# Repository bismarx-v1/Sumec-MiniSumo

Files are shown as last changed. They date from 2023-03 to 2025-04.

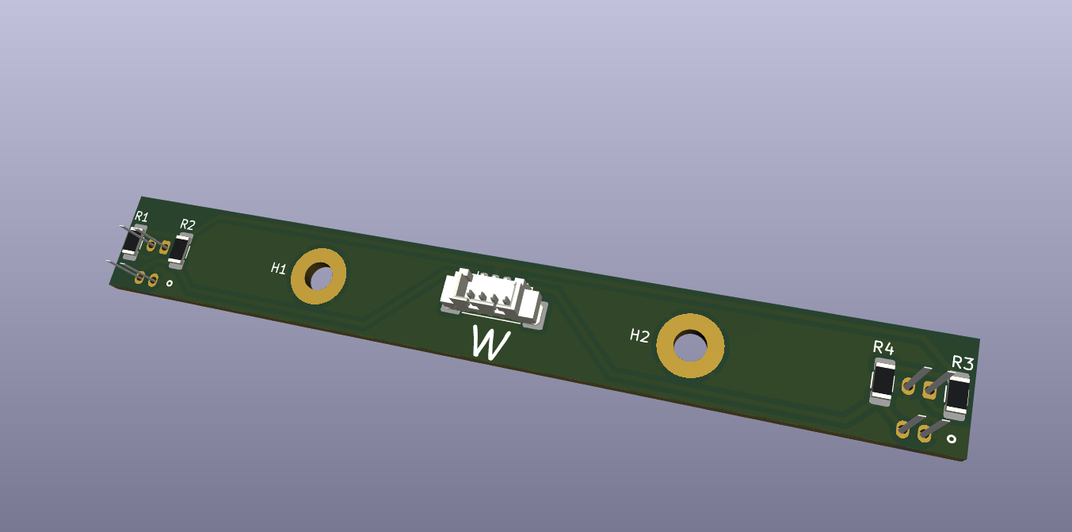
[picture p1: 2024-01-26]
-3D-/el._parts/PCBs/QRE MiniBoards/3D MiniBoards.png

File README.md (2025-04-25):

# THIS IS REPO IS OLD, FOR NEWEST RELAESES VISIT: [Updated repo](https://github.com/bismarx-v1/Sumec-Minisumo-main)

# MiniSumo "SUMEC" Robot Project

## Description
This GitHub repository contains the code and documentation about student-built MiniSumo robot "SUMEC". MiniSumo robots are small autonomous robots designed to compete in MiniSumo competitions, where they attempt to push their opponents out of a ring. Our other repository "Sumec-Remote" is a forked repo from p1rse, created for our own MiniSumo start remote, PCB is ours, schematic was copied from "p1rse/robot-sumo-start-module".
## Contents
- **-3D-** Provides CAD files for the mechanical components of the robot, such as the chassis and sensor mounts.
  
- **-CODE-** Contains the source code for the MiniSumo robot, including firmware for microcontrollers, sensor libraries and control diagrams.
  
- **-DOCS-** Includes robot documentation, rules for specific tournaments, and extras.

- **-PCB-** Includes PCB files, we are using KiCAD for PCB designing.

## Our suppliers
We buy our components from: 

- [Mouser Electronics](https://cz.mouser.com/?utm_id=93841169&gad_source=1)
- [GM Electronics](https://www.gme.cz)
- [TME](https://www.tme.eu/cz/en/)
- [BotLand](https://botland.cz/?gad_source=1)

## Contributing
Contributions to this project are welcome! If you have improvements, bug fixes, or new features to contribute, feel free to contact us!

## Acknowledgements
We would like to thank our school SPŠ na Proseku, our teachers, our principle, for providing resources, knowledge and top-notch equipment.

## Contact
If you have any questions, suggestions, or issues regarding this project, please feel free to contact us: 

Email - savvapopov1804@gmail.com
LinkedIn - www.linkedin.com/in/savva-popov

And follow us on the social media! 
Instagram - @sumec_minisumo_bot

**Sending love, from Czech Republic!**

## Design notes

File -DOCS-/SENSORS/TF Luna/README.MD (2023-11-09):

Configuration input:

GND: I2C
NC/3V3: UART

I2C default address: 0x10 (can be changed)

https://github.com/budryerson/TFLuna-I2C

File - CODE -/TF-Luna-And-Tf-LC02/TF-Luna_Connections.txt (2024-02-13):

=============================================================================
┌──────┐	PCBConnector:	Back = J6
│''''''│	Sensor:		Left
└123456┘
-----------------------------------------------------------------------------
1 - SesorSupply	| 5V
2 - SDA		| ProcessorPin_18
3 - SCL		| ProcessorPin_17
4 - GND		| GND
5 - XShut1	| XS1->0R->GND; (XS2->0R->ProcessorPin_40)
6 - [empty]	| [empty]

=============================================================================
┌──────┐	PCBConnector:	Mid = J7
│''''''│	Sensor:		Mid
└123456┘
-----------------------------------------------------------------------------
1 - SesorSupply	| 5V
2 - SDA		| ProcessorPin_18
3 - SCL		| ProcessorPin_17
4 - GND		| GND
5 - XShut2	| XS2->0R->GND; (XS2->0R->ProcessorPin_41)
6 - [empty]	| [empty]

=============================================================================
┌──────┐	PCBConnector:	Front = J9
│''''''│	Sensor:		Right
└123456┘
-----------------------------------------------------------------------------
1 - SesorSupply	| 5V
2 - SDA		| ProcessorPin_18
3 - SCL		| ProcessorPin_17
4 - GND		| GND
5 - XShut3	| XS3->0R->GND; (XS3->ProcessorPin_42)
6 - [empty]	| [empty]

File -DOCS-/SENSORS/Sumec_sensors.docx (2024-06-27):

# SUMEC Optics

1. Distance measurement

2. Presence of objects

# TF-LUNA 1.

LiDAR Range Sensor / ToF

Distance measured: 8m

Communication protocol: UART/I2C

Output: Digital

Technology: Infrared

Input voltage: Vin = 5V

Connector: Molex PicoBlade

TF-LUNA Manual (https://www.waveshare.com/wiki/TF-Luna_LiDAR_Range_Sensor)

PROS:

- We have 3 of them
- Low FoV: 2°
- Accurate
- We know they work

CONS:

- Cost (500/600Kč)
- Dimensions: 35mm*21.25mm*13.5mm
- Blind zone: 20cm – unreliable measurement
- Harder measurement for objects with high reflectivity

# Pololu Distance Sensor 1.

LiDAR-based Distance Sensor / ToF

Distance measured: 50, 130cm

Communication: Digital Pulse Width

Output: Digital

Technology: Infrared laser

Input voltage: Vin = 3-5V

Connector: 2,54 - 3Pad holes

Polulu Pulse Width manual (https://www.pololu.com/product/4071)

PROS:

- Dimensions: (21.6 × 8.9 × 3.5 mm)
- Accurate

CONS:

- Cost: (400Kč)
- Minimum range: 4 cm (for accurate measurement); < 1 mm (for detection)
- High FoV: 15°
- We don’t know if they work

# VL53L1X 1.

Laser distance measurement sensor / ToF

Distance measured: 400cm max

Communication: I2C

Output: Digital

Technology: Infrared laser

Input voltage: Vin = 3-5V

Connector: 2,54 - Pad holes

VL53L1X Datasheet (https://www.laskakit.cz/user/related_files/vl53l1x.pdf)

PROS:

- Cost: (200Kč)
- Dimensions: 29.5x22mm
- Accuracy 1mm

CONS:

- Programmable FoV from 15 to 27 degrees (?)
- We don’t know if they work

# VL53L3CX 1.

Laser distance measurement sensor / ToF

Distance measured: 300cm max

Communication: I2C

Output: Digital

Technology: Infrared laser

Input voltage: Vin = 2.8-5V

Connector: 2,54 - Pad holes

VL53L3CX (https://cz.mouser.com/datasheet/2/389/vl53l3cx-satel-1858618.pdf)

PROS:

- Dimensions:
- True distance measurement independent of target size and reflectance

CONS:

- Cost: (400Kč)
- We don’t know if they work

# TF-LC02 1.

LiDAR laser distance Sensor / ToF

Distance measured: 200cm

Communication: UART

Output: Digital

Technology: Infrared laser

Input voltage: Vin = 3-3.7V

Connector: JST SH

Polulu Pulse Width manual (https://www.pololu.com/product/4071)

PROS:

- We have 1 of them
- Cost: (250Kč)
- Very small size 20 x 11.5 x 7.6 mm
- Accurate

CONS:

- Minimum range: 3 cm (for accurate measurement)
- High FoV: 18°
- We don’t know if they work
- Almost no documentation

# Pololu Digital Distance Sensor 2.

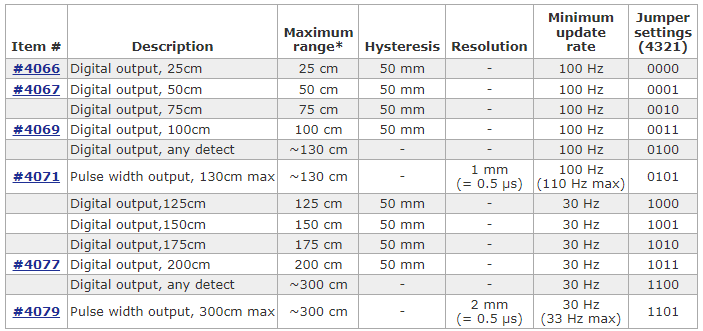
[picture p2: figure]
Obsah obrázku text, snímek obrazovky, číslo, Písmo Popis byl vytvořen automaticky

LiDAR based distance sensor / I/O

Distance measured: 50/100cm

Communication: HIGH/LOW

Output: Digital

Technology: Infrared laser

Input voltage: Vin = 3-5.5V Distance seen is based on the jumper config.

Connector: 2.54, 3 Pad Holes

Polulu digital detection manual (https://www.pololu.com/product/4067)

PROS:

- Size 21.6 × 8.9 × 3.5 mm
- Accurate – 1mm
- Adjustable distance
- Adjustable type of measurement

CONS:

- Cost: (500Kč)
- FoV: 15°
- We don’t know if they work

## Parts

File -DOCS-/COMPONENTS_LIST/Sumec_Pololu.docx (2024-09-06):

# SUMEC Pololu BOM

# Pololu Distance Sensor 1.

LiDAR-based Distance Sensor / ToF

Distance measured: 50, 130cm

Communication: Digital Pulse Width

Output: Digital

Technology: Infrared laser

Input voltage: Vin = 3-5V

Connector: 2,54 - 3Pad holes

Polulu Pulse Width manual (https://www.pololu.com/product/4071)

https://www.pololu.com/product/4064

# 12V 1100RPM HPCB

High power, carbon brushes DC motor

Voltage: 12V

Encoder: Yes (Side)

RPM: 1100

Length: 41mm

Connector: JST SH Female

2X https://www.pololu.com/product/5211

# 12V 650RPM HPCB

High power, carbon brushes DC motor

Voltage: 12V

Encoder: Yes (Side)

RPM: 650

Length: 41mm

Connector: JST SH Female

2x https://www.pololu.com/product/5213

# Pololu Digital Distance Sensor 2.

Obsah obrázku text, snímek obrazovky, číslo, Písmo Popis byl vytvořen automaticky

LiDAR based distance sensor / I/O

Distance measured: 50/100cm

Communication: HIGH/LOW

Output: Digital

Technology: Infrared laser

Input voltage: Vin = 3-5.5V Distance seen is based on the jumper config.

Connector: 2.54, 3 Pad Holes

Polulu digital detection manual (https://www.pololu.com/product/4067)

PROS:

- Size 21.6 × 8.9 × 3.5 mm
- Accurate – 1mm
- Adjustable distance
- Adjustable type of measurement

CONS:

- Cost: (500Kč)
- FoV: 15°
- We don’t know if they work

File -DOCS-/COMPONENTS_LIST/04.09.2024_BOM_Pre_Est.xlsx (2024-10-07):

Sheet: SMD 1206
Footprint | Value | Link | Reserve
1206 | S-DIODE | S-Diode, 2A, 1206, mouser (https://cz.mouser.com/ProductDetail/KYOCERA-AVX/SD1206S040S2R0?qs=jCA%252BPfw4LHbfEJl0sZ31oA%3D%3D) | 1
1206 | 10k |  | 2
1206 | 100R |  | 3
1206 | 15R |  | 5
1206 | 0R |  | 4
1206 | 22uF, Polymer-Tantal | 22uF, 16V, Tantal-Polymer (https://cz.mouser.com/ProductDetail/KYOCERA-AVX/TCJA226M016R0300E?qs=%252B6g0mu59x7JjwGwmiCcXvg%3D%3D) | 6
1206 | 10uF, Polymer-Tantal | 10uF, 25V, Tantal-Polymer (https://cz.mouser.com/ProductDetail/KYOCERA-AVX/TCJA106M025R0150E?qs=hWgE7mdIu5SUx0aLKy2TqQ%3D%3D) | 10
1206 | 10uF, 16V, Tantal | 10uF, 16V, 1206, tantal, mouser (https://cz.mouser.com/ProductDetail/KEMET/T491A106K016AT) | 28 | 6
1206 | 1uF Tantal |  | 8
1206 | 100nF, Ceramic |  | 8

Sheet: SMD 0805
Footprint | Value | Link | Reserve
0805 | RED | Red LED, 20mA 1.9V, 0805, mouser (https://cz.mouser.com/ProductDetail/Stanley-Electric/VFHV1112H-3BZ2B-TR?qs=byeeYqUIh0PKiA%252BYRcKo5Q%3D%3D) | 15
0805 | YELLOW | Yellow LED, 20mA, 1.9V, 0805, mouser (https://cz.mouser.com/ProductDetail/Stanley-Electric/FY1112H-TR?qs=byeeYqUIh0M%2F1I90%252BhjkXg%3D%3D) | 6
0805 | GREEN | Green-Yellow LED, 20mA, 1.9V, mouser (https://cz.mouser.com/ProductDetail/Stanley-Electric/VFHD1112H-3B72B-TR?qs=byeeYqUIh0N1xLw8fV03PA%3D%3D) | 4
0805 | 10k | 10k, 250mW, 0805, mouser (https://cz.mouser.com/ProductDetail/Vishay-Dale/RCC080510K0FKEA?qs=GedFDFLaBXGY93oge9hajw%3D%3D) | <60
0805 | 1k | 1k. 500mW, 0805, mouser (https://cz.mouser.com/ProductDetail/Vishay-Dale/CRCW08051K00FKEAHP?qs=FlFvgi4rxBy%252Bn2DMV%2FkIbA%3D%3D) | 2
0805 | 560R | 560R, 500mW, 0805, mouser (https://cz.mouser.com/ProductDetail/Bourns/CHP0805AFX-5600ELF?qs=GedFDFLaBXHiLkJv9wkGiw%3D%3D) | 18
0805 | 100R | 100R, 0.5W, 0805, mouser (https://cz.mouser.com/ProductDetail/Vishay-Dale/CRCW0805100RFKEAHP?qs=k2%2FDWSARqgHN0DmoUSjg4g%3D%3D) | 10
0805 | 200R | 200R, 500mW, 0805, mouser (https://cz.mouser.com/ProductDetail/Vishay-Dale/CRCW0805200RFKEAHP?qs=2Xec%252BEQj5n%252BcRsKDNXpbZw%3D%3D) | 4
0805 | 15R | 15R, 100mW, 0805,mouser (https://cz.mouser.com/ProductDetail/Panasonic/ERJ-6RED15R0V?qs=KTDjhDDUMAl6Ra4%2FZLG24g%3D%3D) | 16
0805 | 2.2R | 2.2R, 500mW, 0805, mouser (https://cz.mouser.com/ProductDetail/Vishay-Dale/CRCW08052R20FKEAHP?qs=40TFAHZMFvc8altFjF5kRw%3D%3D) | 4
0805 | 100nF | 100nF, 16V, 0805, ceramic, mouser X7R (https://cz.mouser.com/ProductDetail/YAGEO/AC0805KRX7R7BB104) | >60
0805 | 22nF | 22nF, 50V, 0805, ceramic, mouser, X7R (https://cz.mouser.com/ProductDetail/KYOCERA-AVX/08055C223KAT4A)
0805 | 18pF | 18pF, 16V, 0805, ceramic, mouser (https://cz.mouser.com/ProductDetail/KYOCERA-AVX/0805YA180JAT2A?qs=nl0EtZFOfLiGc7H%252BYUnNHw%3D%3D) | 5

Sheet: SMD OTHER
Value | Footprint | Link | Reserve
Conn_01x04_Pin | Molex_PicoBlade_1x04-1MP_P1.25mm_Vertical | Molex PicoBlade, 4 Pin, vertical, mouser | 2
Conn_01x03_Pin | Molex_PicoBlade_1x03-1MP_P1.25mm_Vertical | Molex PicoBlade, 3 Pin, vertical, mouser | 4
Conn_01x06_Pin | Molex_PicoBlade_1x06-1MP_P1.25mm_Vertical | Molex PicoBlade, 6 Pin, vertical, mouser | 1
Conn_01x04_Pin | Molex_PicoBlade_1x04-1MP_P1.25mm_Horizontal | Molex PicoBlade, 4 Pin, horizontal, mouser | 2
TYPE-C-31-M-12 | USB_Type_C | USB C mouser (https://eu.mouser.com/ProductDetail/GCT/USB4105-GF-A-060?qs=QNEnbhJQKvY2mocwNJzgfA%3D%3D) | 4
5V, 5A | TO-252, AZ1084 |  | 2
3V3, 3A | LD1085 |  | 2
LM1084-3.3 | TO-263-3_TabPin2 | LM1084IS-3.3-NOPB, mouser
LM1084-5.0 | TO-263-3_TabPin2 | LM1084IS-5.0-NOPB, mouser
USBLC6-2SC6 | TSOT-23-6_HandSoldering | ESD protekce mouser | 6
SW_Push | SW_SPST_B3U-1000P | B3U-1000P mouser (https://cz.mouser.com/ProductDetail/Omron-Electronics/B3U-1000P?qs=AO7BQMcsEu4ip80xyf2FwA%3D%3D) | 6
QRE1113 | OnSemi_CASE100AQ - QRE1113 | QRE1113 THT mouser (https://cz.mouser.com/ProductDetail/onsemi-Fairchild/QRE1113?qs=ne66E0WZ%2FFkJiYCW1J5zEw%3D%3D) | 10
QRE1113_SMD | QRE1113_SMD |  | 10
MCU | ESP32-S3-WROOM-1 | ESP32 S3 WROOM1 mouser (https://cz.mouser.com/ProductDetail/Espressif-Systems/ESP32-S3-WROOM-1-N4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) | 1
MCU | ESP32-S3-WROOM-2 |  | 3
TB6612FNG | TB6612FNG |  | 8
DRV8874 | DRV8874PWPR | DRV8874. mouser (https://cz.mouser.com/ProductDetail/Texas-Instruments/DRV8874PWPR?qs=mAH9sUMRCtvh%2FSU15ywmDA%3D%3D) | 0
DMG6968U-7 | TSOT-23-3_HandSoldering | NMOS, SOT23-3, mouser (https://eu.mouser.com/ProductDetail/Diodes-Incorporated/DMG6968U-7?qs=oUsD4qhOtFxfxyoeWY4RMA%3D%3D) | 6
DS04-254-1-05BK-SMT | DIP_SWITCH | 5P, 2.54mm, DIP, mouser (https://cz.mouser.com/ProductDetail/CUI-Devices/DS04-254-1-05BK-SMT?qs=wnTfsH77Xs5Ndj%252Bt08dChA%3D%3D) | 1
Crystal - ABM8G | CRYSTAL_SMD | 16 MHz, 18 pF, mouser (https://www.mouser.co.uk/ProductDetail/ABRACON/ABM8G-16.000MHZ-18-D2Y-T?qs=3LVMET7lfiPkoUdIbdKAPg%3D%3D) | 4
YC248-JR-0710KL | RESISTOR_ARRAY | 10k, 8x0402, mouser (https://cz.mouser.com/ProductDetail/YAGEO/YC248-JR-0710KL?qs=8cPjvKtxWv7XgZyJevtvWg%3D%3D) | 8

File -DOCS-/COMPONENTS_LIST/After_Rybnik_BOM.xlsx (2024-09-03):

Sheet: SMD 1206
Footprint | Value | Link | Reserve
1206 | 10k |  | 2
1206 | 100R |  | 3
1206 | 15R |  | 6
1206 | 0R |  | 7
1206 | 10uF? Tantal |  | 10
1206 | 10uF, Ceramic |  | 6
1206 | 10uF, 16V, Tantal | 10uF, 16V, 1206, tantal, mouser (https://cz.mouser.com/ProductDetail/KEMET/T491A106K016AT) | <30
1206 | 1uF Tantal |  | 7
1206 | 100nF |  | 9
1206 | s-diode | S-Diode, 2A, 1206, mouser (https://cz.mouser.com/ProductDetail/KYOCERA-AVX/SD1206S040S2R0?qs=jCA%252BPfw4LHbfEJl0sZ31oA%3D%3D) | 4

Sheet: SMD 0805
Footprint | Value | Link | Reserve
805 | 10k | 10k, 250mW, 0805, mouser (https://cz.mouser.com/ProductDetail/Vishay-Dale/RCC080510K0FKEA?qs=GedFDFLaBXGY93oge9hajw%3D%3D) | 12
805 | 560R | 560R, 500mW, 0805, mouser (https://cz.mouser.com/ProductDetail/Bourns/CHP0805AFX-5600ELF?qs=GedFDFLaBXHiLkJv9wkGiw%3D%3D) | 18
805 | 100R | 100R, 0.5W, 0805, mouser (https://cz.mouser.com/ProductDetail/Vishay-Dale/CRCW0805100RFKEAHP?qs=k2%2FDWSARqgHN0DmoUSjg4g%3D%3D) | 10
805 | 15R | 15R, 100mW, 0805,mouser (https://cz.mouser.com/ProductDetail/Panasonic/ERJ-6RED15R0V?qs=KTDjhDDUMAl6Ra4%2FZLG24g%3D%3D) | 16
805 | 22nF, 50V Ceramic | 22nF, 50V, 0805, ceramic, mouser, X7R (https://cz.mouser.com/ProductDetail/KYOCERA-AVX/08055C223KAT4A) | 15
805 | 100nF, 16V, Ceramic | 100nF, 16V, 0805, ceramic, mouser X7R (https://cz.mouser.com/ProductDetail/YAGEO/AC0805KRX7R7BB104) | <80
805 | RED | Red LED, 20mA 1.9V, 0805, mouser (https://cz.mouser.com/ProductDetail/Stanley-Electric/VFHV1112H-3BZ2B-TR?qs=byeeYqUIh0PKiA%252BYRcKo5Q%3D%3D)
805 | YELLOW | Yellow LED, 20mA, 1.9V, 0805, mouser (https://cz.mouser.com/ProductDetail/Stanley-Electric/FY1112H-TR?qs=byeeYqUIh0M%2F1I90%252BhjkXg%3D%3D) |  | 8,8,18
805 | GREEN-YELLOW | Green-Yellow LED, 20mA, 1.9V, mouser (https://cz.mouser.com/ProductDetail/Stanley-Electric/VFHD1112H-3B72B-TR?qs=byeeYqUIh0N1xLw8fV03PA%3D%3D)

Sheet: SMD OTHER
Footprint | Value | Link | Reserve
Molex_PicoBlade_53398-0471_1x04-1MP_P1.25mm_Vertical | Conn_01x04_Pin | Molex PicoBlade, 4 Pin, vertical, mouser | 2
Molex_PicoBlade_53398-0371_1x03-1MP_P1.25mm_Vertical | Conn_01x03_Pin | Molex PicoBlade, 3 Pin, vertical, mouser | 4
Molex_PicoBlade_53398-0671_1x06-1MP_P1.25mm_Vertical | Conn_01x06_Pin | Molex PicoBlade, 6 Pin, vertical, mouser | 1
Molex_PicoBlade_53261-0471_1x04-1MP_P1.25mm_Horizontal | Conn_01x04_Pin | Molex PicoBlade, 4 Pin, horizontal, mouser | 2
USB_Type_C | TYPE-C-31-M-12 | USB C mouser | 6
TO-252 | 5V, 5A max 12V |  | 2
LD1085 | 3v3, 3A |  | 2
TO-263-3_TabPin2 | LM1084-3.3 | LM1084IS-3.3-NOPB, mouser | 1
TO-263-3_TabPin2 | LM1084-5.0 | LM1084IS-5.0-NOPB, mouser | 1
TSOT-23-6_HandSoldering | USBLC6-2SC6 | ESD protekce mouser
ESP32-S3-WROOM-1 | ESP32-S3-WROOM-1 | ESP32 S3 WROOM1 mouser (https://cz.mouser.com/ProductDetail/Espressif-Systems/ESP32-S3-WROOM-1-N4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) | 1
DRV8874 | DRV8874PWPR | DRV8874. mouser (https://cz.mouser.com/ProductDetail/Texas-Instruments/DRV8874PWPR?qs=mAH9sUMRCtvh%2FSU15ywmDA%3D%3D) | 1
esp32 s3 wroom2 | esp32 s3 wroom2 |  | 3
SW_SPST_B3U-1000P | SW_Push | B3U-1000P mouser (https://cz.mouser.com/ProductDetail/Omron-Electronics/B3U-1000P?qs=AO7BQMcsEu4ip80xyf2FwA%3D%3D) | 6
OnSemi_CASE100AQ - QRE1113 | QRE1113 | QRE1113 THT mouser (https://cz.mouser.com/ProductDetail/onsemi-Fairchild/QRE1113?qs=ne66E0WZ%2FFkJiYCW1J5zEw%3D%3D) | 6
qre smd | qresmd |  | 10
TB6612FNG |  |  | 8

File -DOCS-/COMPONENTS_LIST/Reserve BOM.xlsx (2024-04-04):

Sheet: el. components - THD
EL. COMPONENTS
QTY in use | QTY reserve | lost | NAME | VALUE | CODE | COST (1pc) | SUPPLIER
2 | 1 |  | stabilizer | 3v3 3a | lm1085
0 | 3 |  | stabilizer | 3v3 5a | lm1084 |  |  | 1
 | 2 |  | stabilizer | 3v3 1a | ld1117av33 |  |  | 1
0 | 4 |  | stabilizer | 5v 1a5 | UA7805C
0 | 3 |  | stabilizer | 3v3 0,8a | ld33v |  |  | 1
 | 21 |  | resistor | 10k
 | 16 |  | resistor | 100
 |  |  | resistor | 82
 |  |  | resistor | 68
 | 14 |  | cappacitor | 0,1µF 100V |  |  |  | 1
 | 12 |  | cappacitor | 10µF 16V |  |  |  | 1
 | 11 |  | cappacitor | 22µF 16V |  |  |  | 1
 | 5 |  | schottky diode | 1A |  |  |  | 1
 | 5 |  | schottky diode | 3A |  |  |  | 1
 | 13 |  | LED | multi color
6 | 4 |  | button
1 | 2 |  | ir recever |  | tsop382
6 | 2 |  | laser sensor
8 | 19 |  | qre tht
 | 6 |  | 3pin conector M
 | 6 |  | 3pin conector F
0 | 3 |  | ir recever | 2,5-5,5V 38kH | TSOP31138 |  | mouser | 1
0 | 1 |  | usb-c 4-pin
0 | 2 |  | regulátor nap. | 5V 3A pos. | ld1085V50 |  | mouser
 |  |  | mosfet |  | irf520 |  |  | 1

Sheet: el. components - SMD
EL. COMPONENTS
QTY in use | QTY reserve | lost | NAME | VALUE | CODE | COST (1pc) | SUPPLIER
 | ? | 1 | esp32 s3 vrum1
 | 3 |  | esp32 s3 vrum2 |  |  |  |  | 1
 | 8 | 1 | brush motor driver |  | TB6612FNG |  | mouser | 1
 | 1 |  | h-bridge m |  | drv8874pwpr |  | mouser | 1
 | 6 | 1 | elektrostatická ochrana |  | USBLC6-2SC6 |  | mouser | 1
0 | 10 |  | tantalový kondenzátor | 25V 106 20% | TCJA106M025R0150E |  | mouser | 1
 | 6 |  | tantalový kondenzátor | 16V 226 20% | TCJA226M016R0300E |  | mouser | 1
 | 8 |  | tantalový kondenzátor | 16V 1µF | T491A105K016AT |  | mouser | 1
 | 45 |  | tantalový kondenzátor | 16V 10µF |  |  | mouser | 1
 | 6 |  | keramický kondenzátor | 16v 10µF | KAF31GR71C106KU |  | mouser | 1
 | ? |  | keramický kondenzátor | 25V 100nF | 12063C104JAT2A |  | mouser
 |  |  | keramický kondenzátor | 50v 22nf | 08055c223kat4a |  | mouser | 1
 | cca 98 |  | keramický kondenzátor | 16v 0,1µF | ac0805krx7r7bb104 |  | mouser | 1
0 | 1 |  | laserowy czujnik |  | TF-LC02 |  |  | 1
 | 6 |  | čudlíci NO |  | b3u-1000p |  | mouser | 1
 | 4 |  | JST SH 1mm 6-pin konektor 90°
 | 10 |  | JST SH 1mm 6-pin konektor rovný
 | 4 |  | shotkyho dioda |  | CD1206-B260 |  | mouser | 1
 | 7 |  | rezistor | 0Ω | CRCW12060000ZSTC |  | mouser | 1
 | ? |  | rezistor | 100Ω 0,25W .1% | RT1206BRD07100RL |  | mouser
 | 2 |  | tenkovrství rezistor | 10kΩ | ERA-8BRB1002V |  | mouser | 1
 | 3 |  | tenkovrství rezistor | 100kΩ | tr1206brd07100rt |  | mouser | 1
 | 16 |  | tlustovrství rezistor | 15r | erj-6red15r0v |  | mouser | 1
 | 18 |  | tlustovrství rezistor | 650r | chpp0805afx-5600elf |  | mouser | 1
 | 10 |  | tlustovrství rezistor | 100Ω 0,5W 1% | crcw0805100rfkeahp |  | mouser | 1
 | 6 |  | tlustovrství rezistor | 150Ω 0,25W 5% | AC1206JR-0715RL |  | mouser | 1
 | 12 |  | tlustovrství rezistor | 10k .25w 1% | rcc080510k0fkea |  | mouser | 1
a | 10 |  | qre |  | qre1113 |  |  | 1
 | 5 | 1 | USB-C - F |  |  |  |  | 1
2 | 2 |  | tranzistor | 20v | TSM2302CX RF |  |  | 1
 | 1 |  | stabilizer | 5v 5a | lm1084 |  |  | 1
 | 1 |  | stabilizer | 3v3 5a | lm1084-3v3 |  |  | 1
0 | 2 |  | regulátor nap. | 3.3V 3A pos. | LD1085D2M33R |  | mouser | 1
 | 2 | 1 | regulátor nap. |  | AZ1084CD-5.0TRG1 |  | mouser | 1
 | 10 |  | LED | red | vfhd1112h-3b72b-tr |  | mouser | 1
 | 18 |  | LED |  | vfhv1112h-3bz2b-tr |  | mouser | 1
 | 8 |  | LED | yellow | fy1112hh-tr |  | mouser | 1
 | 1 |  | PicoBlade | 6p. 1.25 F | 53368-4006 |  | mouser | 1
 | 4 |  | PicoBlade | 3p. 1.25 F | 53398-4003 |  | mouser | 1
 | 2 |  | PicoBlade - flat | 4p. 1.25 F | 53261- |  | mouser | 1

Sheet: el. components - other
EL. COMPONENTS
QTY in use | QTY reserve | lost | NAME | VALUE | CODE | COST (1pc) | SUPPLIER
0 | 1 |  | esp32-s3-devkitC-1
0 | 4 |  | H bridge
1 | 1 |  | esp32-vrum32-devkit-1
0 | 1 |  | arduino UNO
0 | 1 |  | arduino NANO
1 | 2 | 2 | circuit board mk2
3 | 2 |  | XT-30 M
4 | 6 |  | XT-30 F
0 | 1 |  | jet switch
0 | 2 |  | lever switch
2 | 1 |  | switch screwable | 2A
3 | 2 |  | switch
 | 4 |  | DC motor | 12V 150rpm
 | 4 |  | DC motor | 12V 300rpm
 | 0 |  | battery | 8,4v 450mAh
 | 1 |  | battery | 12,6V 450mAh
 | 1 |  | terrorist battery 2s | ???
 | 3 |  | TF-Luna | 5V
 |  |  | 0

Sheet: mechanics
MECHANICS
QTY in use | QTY reserve | lost | NAME | VALUE | CODE | COST (1pc) | SUPPLIER
2 |  |  | jsumo wheel - core
2 |  |  | jsumo wheel - tire
2 |  |  | custom wheels - core
 | 30 |  | heta isert | M3
 | 2 |  | všesměrová koule

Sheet: tools + other
TOOLS
QTY in use | QTY reserve | lost | NAME | VALUE | CODE | COST (1pc) | SUPPLIER
1 |  |  | battery tester
1 |  |  | IR controller
 | 1 |  | USB-A na USB-B kabel
 | 1 |  | posuvné měřítko
 |  |  | li-pol guard
 |  |  | thermal compound
 | 1 |  | t10 klíč
 | 3 |  | cr2025 batt

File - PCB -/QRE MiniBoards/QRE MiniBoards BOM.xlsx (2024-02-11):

Item | Reference(s) | Footprint | Qty | Value | Supplier and ref
1 | H1,H2 | MountingHole_3.2mm_M3_Pad | 2 | M3
2 | R3,R1 | R_0805_2012Metric_Pad1.20x1.40mm_HandSolder | 2 | 100
3 | R4,R2 | R_0805_2012Metric_Pad1.20x1.40mm_HandSolder | 2 | 10k
4 | J2 | Molex_PicoBlade_53261-0471_1x04-1MP_P1.25mm_Horizontal | 1 | Conn_01x04_Pin
5 | U2,U1 | OnSemi_CASE100AQ - QRE1113 | 2 | QRE1113
 |  |  | 9

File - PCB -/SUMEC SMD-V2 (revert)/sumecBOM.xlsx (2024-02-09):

Id | Designator | Footprint | Quantity | Designation | Supplier and ref
1 | IC2,IC3 | DRV8874 | 2 | DRV8874PWPR
2 | SW1,SW3,SW2 | SW_SPST_B3U-1000P | 3 | SW_Push
3 | R3 | R2D2 | 1 | R
4 | H1,H3,H2 | MountingHole_3.2mm_M3_Pad | 3 | MountingHole_Pad
5 | J2 | SolderWire-0.1sqmm_1x01_D0.4mm_OD1mm | 1 | Conn_01x01_Pin
6 | U4 | TO-263-3_TabPin2 | 1 | LM1084-5.0
7 | C18,C1 | C_0805_2012Metric_Pad1.18x1.45mm_HandSolder | 2 | 22nF.hb
8 | C17,C6 | C_0805_2012Metric_Pad1.18x1.45mm_HandSolder | 2 | 100nF.hb
9 | C13,C11,C12,C10 | CP_EIA-2012-12_Kemet-R_Pad1.30x1.05mm_HandSolder | 4 | 10uF.stabl
10 | R2,R1 | R_0805_2012Metric_Pad1.20x1.40mm_HandSolder | 2 | 220
11 | J5 | USB_Type_C | 1 | TYPE-C-31-M-12
12 | C7 | C_0805_2012Metric_Pad1.18x1.45mm_HandSolder | 1 | 100nF.en
13 | C16,C5 | CP_EIA-2012-12_Kemet-R_Pad1.30x1.05mm_HandSolder | 2 | 10uF.hb
14 | D3 | D_0805_2012Metric_Pad1.15x1.40mm_HandSolder | 1 | D_Schottky
15 | R7 | R_0805_2012Metric_Pad1.20x1.40mm_HandSolder | 1 | 10k.mcu
16 | R6,R5 | R_0805_2012Metric_Pad1.20x1.40mm_HandSolder | 2 | 15R
17 | D2,D1 | LED_0805_2012Metric_Pad1.15x1.40mm_HandSolder | 2 | LED
18 | U1 | TO-263-3_TabPin2 | 1 | LM1084-3.3
19 | C9 | C_0805_2012Metric_Pad1.18x1.45mm_HandSolder | 1 | 100nF
20 | J7,J6,J8 | Molex_PicoBlade_53398-0671_1x06-1MP_P1.25mm_Vertical | 3 | Conn_01x06_Pin
21 | IC1 | XT30U-M_1x02_P5.0mm_Vertical | 1 | XT30U-F
22 | U3 | TSOT-23-6_HandSoldering | 1 | USBLC6-2SC6
23 | U2 | ESP32-S3-WROOM-1 | 1 | ESP32-S3-WROOM-1
24 | U5 | TSOP | 1 | TSOP382xx
25 | R8 | Logo | 1 | R
26 | C8 | C_0805_2012Metric_Pad1.18x1.45mm_HandSolder | 1 | 100nF.boot
27 | SW4 | Custom_SPDT_4.8mm_Switch | 1 | SW_DPDT_x2
28 | C3 | CP_EIA-2012-12_Kemet-R_Pad1.30x1.05mm_HandSolder | 1 | 10uF.mcu
29 | J4,J10,J9 | Molex_PicoBlade_53398-0371_1x03-1MP_P1.25mm_Vertical | 3 | Conn_01x03_Pin
30 | C4 | C_0805_2012Metric_Pad1.18x1.45mm_HandSolder | 1 | 100nF.mcu
31 | R4 | R_0805_2012Metric_Pad1.20x1.40mm_HandSolder | 1 | 0R
32 | C19,C2 | C_0805_2012Metric_Pad1.18x1.45mm_HandSolder | 2 | 220nF.hb
33 | J1 | JST_XH_B4B-XH-A_1x04_P2.50mm_Vertical | 1 | Conn_01x04_Pin
34 | C15,C14 | CP_EIA-2012-12_Kemet-R_Pad1.30x1.05mm_HandSolder | 2 | 10uF.shrp
35 | R9 | R_0805_2012Metric_Pad1.20x1.40mm_HandSolder | 1 | 10k
36 | J3 | Molex_PicoBlade_53398-0471_1x04-1MP_P1.25mm_Vertical | 1 | Conn_01x04_Pin
37 | R10 | R_0805_2012Metric_Pad1.20x1.40mm_HandSolder | 1 | 100

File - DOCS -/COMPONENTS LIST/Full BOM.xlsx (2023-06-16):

QTY | VALUE | COMPONENT | COST | DO WE HAVE IT?
2 | 10uF | Cappacitor |  | 9
1 | RED | LED | 0 | YES
1 | D_Schottky | Diode |  | 2
3 | M3 | Mounting Hole |  | 30
1 | XT30U-F | Battery conneector |  | 2F and 2M
1 | 75 | Resistor
4 | 100 | Resistor |  | 6
4 | 10k | Resistor |  | 10
1 | SW_SPDT | Switch (3 pin header) |  | 2 types 8 in total
1 | SW_Push | Button | 0 | YES
1 | ESP32-DEVKIT-V1 | MCU |  | 3
3 | VL53L0X | Laser Sensor |  | 4
1 | TSOP382xx | IR Sensor |  | 1 module,
4 | QRE1113 | Line Rensor |  | 10 smd 11 thd
1 | LD1117AV33 | Stabiliastor |  | 2
1 | ROB-14450 | Motor Driver |  | 4+1
15x2 | 2,54mm | Pin Header
8x2 | 2,54mm | Pin Header
3 | CUSTOM MADE | Laser sensor connector
2 | 12V 150/300/500 RPM | DC Motors |  | 8
1 | 450mAh, 12,6V full charge | Battery/Terrorist battery |  | 1+1
2 | JSUMO | Silicon wheels |  | 3
2 | JSUMO/Custom made | Aluminuim wheels |  | 2+2
1 | Tester | Battery Tester |  | 1

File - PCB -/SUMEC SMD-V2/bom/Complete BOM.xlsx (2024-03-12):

Id | Designator | Quantity | Footprint | Value | Link | Reserve | Quantity
1 | R3 | 1 | R_0805_2012Metric_Pad1.20x1.40mm_HandSolder | 560R | 560R, 500mW, 0805, mouser (https://cz.mouser.com/ProductDetail/Bourns/CHP0805AFX-5600ELF?qs=GedFDFLaBXHiLkJv9wkGiw%3D%3D) | 20 | 1
2 | R5 | 1 | R_1206_3216Metric_Pad1.30x1.75mm_HandSolder | 0R | 0R, 250mW, 1206, mouser (https://cz.mouser.com/ProductDetail/Vishay-Dale/CRCW12060000ZSTC?qs=y5m63dMNjqu0KlgPSWR0ZQ%3D%3D) | 14 | 1
3 | R7,R6 | 2 | R_0805_2012Metric_Pad1.20x1.40mm_HandSolder | 15R | 15R, 100mW, 0805,mouser (https://cz.mouser.com/ProductDetail/Panasonic/ERJ-6RED15R0V?qs=KTDjhDDUMAl6Ra4%2FZLG24g%3D%3D) | 20 | 2
4 | R9,R8 - R4,R2 | 4 | R_0805_2012Metric_Pad1.20x1.40mm_HandSolder | 10k | 10k, 250mW, 0805, mouser (https://cz.mouser.com/ProductDetail/Vishay-Dale/RCC080510K0FKEA?qs=GedFDFLaBXGY93oge9hajw%3D%3D) | 20 | 4
5 | R1,R2,R10 - R3,R1 | 5 | R_0805_2012Metric_Pad1.20x1.40mm_HandSolder | 100R | 100R, 0.5W, 0805, mouser (https://cz.mouser.com/ProductDetail/Vishay-Dale/CRCW0805100RFKEAHP?qs=k2%2FDWSARqgHN0DmoUSjg4g%3D%3D) | 20 | 5
6 | R20, R21 | 2 | R2D2, Logo | R |  |  | 2
7 | C3,C4 | 2 | C_0805_2012Metric_Pad1.18x1.45mm_HandSolder | 22nF.hb | 22nF, 50V, 0805, ceramic, mouser, X7R (https://cz.mouser.com/ProductDetail/KYOCERA-AVX/08055C223KAT4A) | 20 | 2
8 | C2,C13,C5,C6,C7,C8,C11,C12 | 8 | C_0805_2012Metric_Pad1.18x1.45mm_HandSolder | 100nF | 100nF, 16V, 0805, ceramic, mouser X7R (https://cz.mouser.com/ProductDetail/YAGEO/AC0805KRX7R7BB104) | 100? | 8
9 | C1,C9,C10,C15,C14,C19,C17,C18,C16 | 9 | CP_EIA-3216-18_Kemet-A_Pad1.58x1.35mm_HandSolder | 10uF | 10uF, 16V, 1206, tantal, mouser (https://cz.mouser.com/ProductDetail/KEMET/T491A106K016AT) | 50? | 9
10 | D1 | 1 | LED_0805_2012Metric_Pad1.15x1.40mm_HandSolder | LED | Red LED, 20mA 1.9V, 0805, mouser (https://cz.mouser.com/ProductDetail/Stanley-Electric/VFHV1112H-3BZ2B-TR?qs=byeeYqUIh0PKiA%252BYRcKo5Q%3D%3D) | 10 | 1
11 | D2 | 1 | LED_0805_2012Metric_Pad1.15x1.40mm_HandSolder | LED | Yellow LED, 20mA, 1.9V, 0805, mouser (https://cz.mouser.com/ProductDetail/Stanley-Electric/FY1112H-TR?qs=byeeYqUIh0M%2F1I90%252BhjkXg%3D%3D) | 10 | 1
12 | D4 | 1 | LED_0805_2012Metric_Pad1.15x1.40mm_HandSolder | LED | Green-Yellow LED, 20mA, 1.9V, mouser (https://cz.mouser.com/ProductDetail/Stanley-Electric/VFHD1112H-3B72B-TR?qs=byeeYqUIh0N1xLw8fV03PA%3D%3D) | 20 | 1
13 | D3 | 1 | D_1206_3216Metric_Pad1.42x1.75mm_HandSolder | D_Schottky | S-Diode, 2A, 1206, mouser (https://cz.mouser.com/ProductDetail/KYOCERA-AVX/SD1206S040S2R0?qs=jCA%252BPfw4LHbfEJl0sZ31oA%3D%3D) | 6 | 1
14 | J1 | 1 | JST_XH_B4B-XH-A_1x04_P2.50mm_Vertical | Conn_01x04_Pin |  |  | 1
15 | J2 | 1 | SolderWire-0.1sqmm_1x01_D0.4mm_OD1mm | Conn_01x01_Pin |  |  | 1
16 | J9 | 1 | Molex_PicoBlade_53398-0471_1x04-1MP_P1.25mm_Vertical | Conn_01x04_Pin | Molex PicoBlade, 4 Pin, vertical, mouser (https://cz.mouser.com/ProductDetail/Molex/53398-4004?qs=iLbezkQI%252Bsg1CAiQuTsV2g%3D%3D) | 4 | 1
17 | J10,J8,J7 | 3 | Molex_PicoBlade_53398-0371_1x03-1MP_P1.25mm_Vertical | Conn_01x03_Pin | Molex PicoBlade, 3 Pin, vertical, mouser (https://cz.mouser.com/ProductDetail/Molex/53398-4003?qs=iLbezkQI%252BsgbJ%252BQuAD0UPA%3D%3D) | 4 | 3
18 | J2 | 1 | Molex_PicoBlade_53261-0471_1x04-1MP_P1.25mm_Horizontal | Conn_01x04_Pin | Molex PicoBlade, 4 Pin, horizontal, mouser (https://cz.mouser.com/ProductDetail/Molex/53261-0471?qs=%252B72YyncTwW9e3et3PwnEMw%3D%3D) | 4 | 1
19 | J5,J4,J6 | 3 | Molex_PicoBlade_53398-0671_1x06-1MP_P1.25mm_Vertical | Conn_01x06_Pin | Molex PicoBlade, 6 Pin, vertical, mouser (https://cz.mouser.com/ProductDetail/Molex/53398-4006?qs=iLbezkQI%252BsgN7NG7c%2FlBfQ%3D%3D) | 7 | 3
20 | J3 | 1 | USB_Type_C | TYPE-C-31-M-12 | USB C mouser (https://cz.mouser.com/ProductDetail/GCT/USB4105-GF-A-060?qs=QNEnbhJQKvY2mocwNJzgfA%3D%3D&mgh=1) | 6 | 1
21 | U5 | 1 | TO-263-3_TabPin2 | LM1084-3.3 | LM1084IS-3.3-NOPB, mouser (https://cz.mouser.com/ProductDetail/Texas-Instruments/LM1084IS-3.3-NOPB?qs=X1J7HmVL2ZFUeOCa1Tl3Aw%3D%3D) | 3 | 1
22 | U4 | 1 | TO-263-3_TabPin2 | LM1084-5.0 | LM1084IS-5.0-NOPB, mouser (https://cz.mouser.com/ProductDetail/Texas-Instruments/LM1084IS-5.0-NOPB?qs=X1J7HmVL2ZHfHNZJcHduDA%3D%3D) | 3 | 1
23 | U2 | 1 | TSOT-23-6_HandSoldering | USBLC6-2SC6 | ESD protekce mouser (https://cz.mouser.com/ProductDetail/STMicroelectronics/USBLC6-2SC6?qs=po45yt2pPpu%2FhNIlwQdTlg%3D%3D) | 8 | 1
24 | U1 | 1 | ESP32-S3-WROOM-1 | ESP32-S3-WROOM-1 | ESP32 S3 WROOM1 mouser (https://cz.mouser.com/ProductDetail/Espressif-Systems/ESP32-S3-WROOM-1-N4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) | 3 | 1
25 | U3 | 1 | TSOP | TSOP382xx | TSOP382. 38kHz mouser (https://cz.mouser.com/ProductDetail/Vishay-Semiconductors/TSOP38238?qs=RzxYCzJDjPVjpHVZS582Ng%3D%3D) |  | 1
26 | J11 | 1 | AMASS_XT30PW-M | XT30PW-M | XT30PW, horizontal, TME (https://www.tme.eu/en/details/xt30pw-m/dc-power-connectors/amass/) | 5 | 1
27 | IC1,IC2 | 2 | DRV8874 | DRV8874PWPR | DRV8874. mouser (https://cz.mouser.com/ProductDetail/Texas-Instruments/DRV8874PWPR?qs=mAH9sUMRCtvh%2FSU15ywmDA%3D%3D) | 5 | 2
28 | SW1,SW4,SW3 | 3 | SW_SPST_B3U-1000P | SW_Push | B3U-1000P mouser (https://cz.mouser.com/ProductDetail/Omron-Electronics/B3U-1000P?qs=AO7BQMcsEu4ip80xyf2FwA%3D%3D) | 12 | 3
29 | SW2 | 1 | Custom_SPDT_4.8mm_Switch | SW_DPDT_x2 | SPDT Switch, mouser (https://cz.mouser.com/ProductDetail/E-Switch/500SSP3S2M2QEA) |  | 1
30 | H1,H3,H2 - H1, H2 | 5 | MountingHole_3.2mm_M3_Pad | MountingHole_Pad |  |  | 5
31 | U2,U1 | 3 | OnSemi_CASE100AQ - QRE1113 | QRE1113 | QRE1113 THT mouser (https://cz.mouser.com/ProductDetail/onsemi-Fairchild/QRE1113?qs=ne66E0WZ%2FFkJiYCW1J5zEw%3D%3D) | 15 + 4 pujceno + 10 doma | 3
 |  | 2 | CONNECTOR 1x3 | Sharp GP2Y0D810Z0F | SHARP Digital, Side senzor, Botland (https://botland.cz/digitalni-snimace-vzdalenosti/1623-sharp-gp2y0d810z0f-digitalni-snimac-vzdalenosti-10-cm-se-zasuvkou-na-pcb-pololu-1134-5904422305932.html) |  | 2
 |  | 71

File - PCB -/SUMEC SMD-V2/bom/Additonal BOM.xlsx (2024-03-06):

Id | Designator | Qty | Footprint | Value | Link | Reserve | Quantity to order
1 | J8,J7 | 2 | SHARP1-2, 3PIN | Conn_01x03_Pin | PicoBlade, 3P, 75mm, Female to Blunt (https://cz.mouser.com/ProductDetail/Molex/218112-0300?qs=QNEnbhJQKva%2Fzwq48R2atA%3D%3D) |  | 6
2 | J10 | 1 | QRE SNGL, 3PIN | Conn_01x03_Pin | PicoBlade, 3P, 75mm, Female to Blunt (https://cz.mouser.com/ProductDetail/Molex/218112-0300?qs=QNEnbhJQKva%2Fzwq48R2atA%3D%3D)
3 | J9 | 1 | MAIN BRD TO QRE MINIBRD MALE, 4PIN | Conn_01x04_Pin | PicoBlade, 4P, 100mm, Female to Female (https://cz.mouser.com/ProductDetail/Molex/15134-0401?qs=lQAVKuKFhkKhGB2D3%252BUAcg%3D%3D) |  | 2
4 | J5,J4,J6 | 3 | TF-LUNA, MALE, 6PIN | Conn_01x06_Pin | PicoBlade, 6P, 100mm Female to Female (https://cz.mouser.com/ProductDetail/Molex/15134-0601?qs=lQAVKuKFhkKZ3d51CS44yQ%3D%3D) |  | 6
5 | SW2 | 1 | Custom_SPDT_4.8mm_Switch | SW_DPDT_x2 | SPDT Switch (https://cz.mouser.com/ProductDetail/E-Switch/500SSP3S4M6QEB?qs=f57gQzlyLip2q9oLHFusmQ%3D%3D) |  | 2

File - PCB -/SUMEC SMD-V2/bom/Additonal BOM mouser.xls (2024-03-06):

Mfr Part Number (Input) | Manufacturer Part Number | Mouser Part Number | Manufacturer Name | Description | Quantity 1 | Unit Price 1 | Quantity 2 | Unit Price 2 | Quantity 3 | Unit Price 3 | Quantity 4 | Unit Price 4 | Quantity 5 | Unit Price 5 | Order Quantity | Order Unit Price | Min./Mult. | Availability | Lead Time in Days | Lifecycle | NCNR | RoHS | Pb Free | Package Type | Datasheet URL | Product Image | Design Risk
 |  | 538-218112-0300 |  |  | 6
 |  | 538-15134-0401 |  |  | 2
 |  | 538-15134-0601 |  |  | 6
 |  | 612-500SSP3S4M6QEB |  |  | 2

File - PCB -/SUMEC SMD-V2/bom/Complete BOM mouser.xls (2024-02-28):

Mfr Part Number (Input) | Manufacturer Part Number | Mouser Part Number | Manufacturer Name | Description | Quantity 1 | Unit Price 1 | Quantity 2 | Unit Price 2 | Quantity 3 | Unit Price 3 | Quantity 4 | Unit Price 4 | Quantity 5 | Unit Price 5 | Order Quantity | Order Unit Price | Min./Mult. | Availability | Lead Time in Days | Lifecycle | NCNR | RoHS | Pb Free | Package Type | Datasheet URL | Product Image | Design Risk
 |  | 652-CHP0805AFX-5600L |  |  | 10
 |  | 667-ERJ-6RED15R0V |  |  | 10
 |  | 71-RCC080510K0FKEA |  |  | 10
 |  | 71-CRCW0805100RFKEAH |  |  | 10
 |  | 581-08055C223KAT4A |  |  | 10
 |  | 603-AC805KRX7R7BB104 |  |  | 25
 |  | 80-T491A106K016 |  |  | 25
 |  | 327-VFHV1112H3BZ2BTR |  |  | 5
 |  | 327-FY1112HTR |  |  | 5
 |  | 327-VFHD1112H3B72BTR |  |  | 5
 |  | 538-53398-4004 |  |  | 3
 |  | 538-53398-4003 |  |  | 6
 |  | 538-53261-0471 |  |  | 3
 |  | 538-53398-4006 |  |  | 6
 |  | 640-USB4105-GF-A-060 |  |  | 5
 |  | 926-LM1084IS-3.3NOPB |  |  | 3
 |  | 926-LM1084IS50NOPB |  |  | 3
 |  | 356-ESP32-S3WROOM1N4 |  |  | 3
 |  | 595-DRV8874PWPR |  |  | 5
 |  | 653-B3U-1000P |  |  | 10
 |  | 612-500SSP3S2M2QEA |  |  | 3

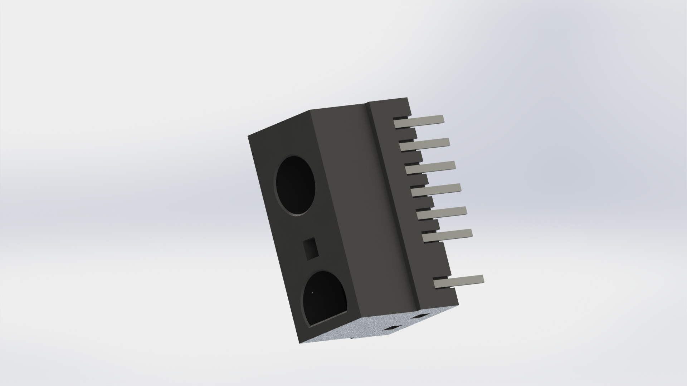
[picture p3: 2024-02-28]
-3D-/el._parts/SensorSharpDigital/Renderings/sharp ir sensor.JPG

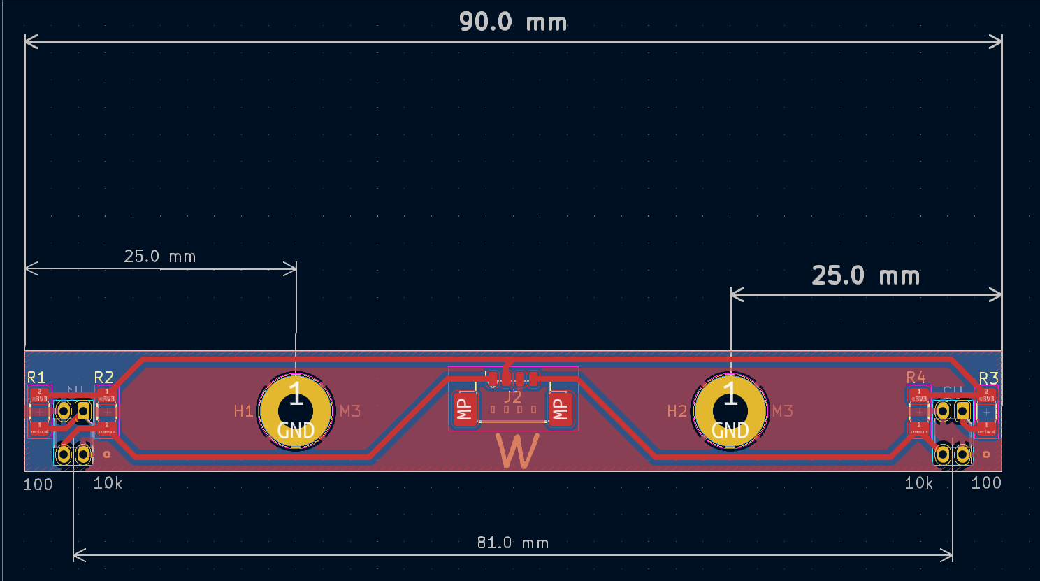
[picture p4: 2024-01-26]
-3D-/el._parts/PCBs/QRE MiniBoards/Dimensions MiniBoards.png

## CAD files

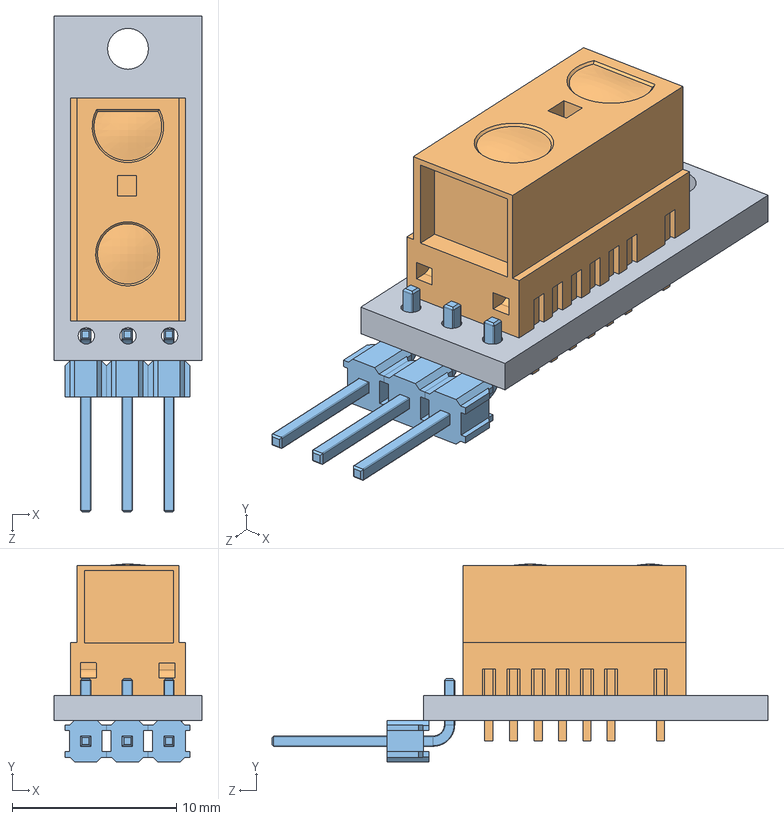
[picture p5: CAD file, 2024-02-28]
-3D-/el._parts/SensorSharpDigital/SensorSharpDigital.SLDASM
9.00 x 12.1 x 30.2 mm
Base
GP2Y0D810Z0F sharp
PIN3Angulo

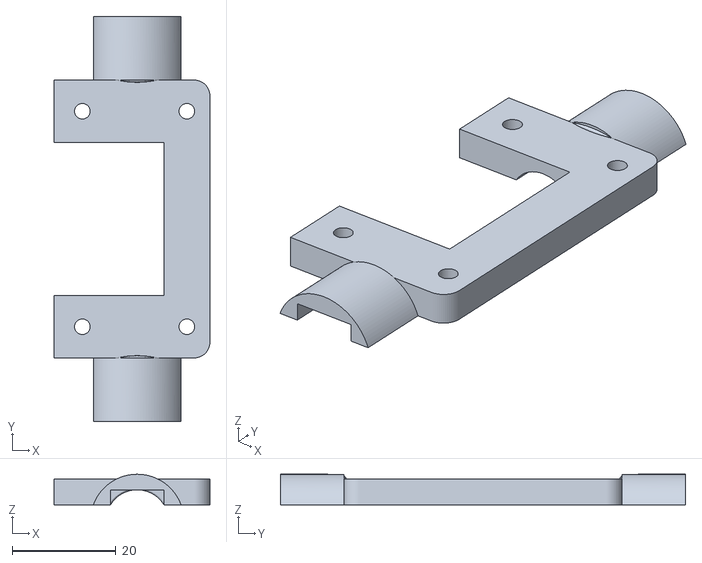
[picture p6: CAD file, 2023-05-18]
- 3D -/domov důchodců/sumec_2.2_body/Objímka motoru.stl
30.0 x 78.0 x 5.88

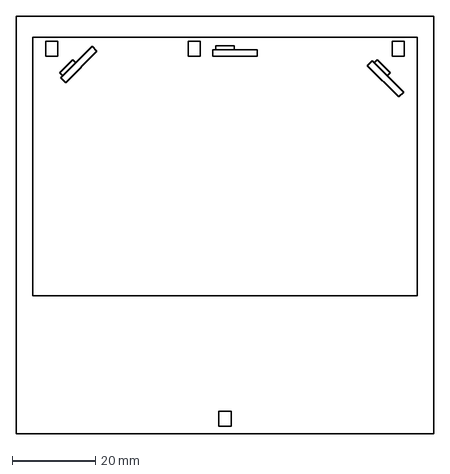
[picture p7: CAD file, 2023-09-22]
- 3D -/wip/Rozložení PCB.dxf
100.0 x 100.0 mm

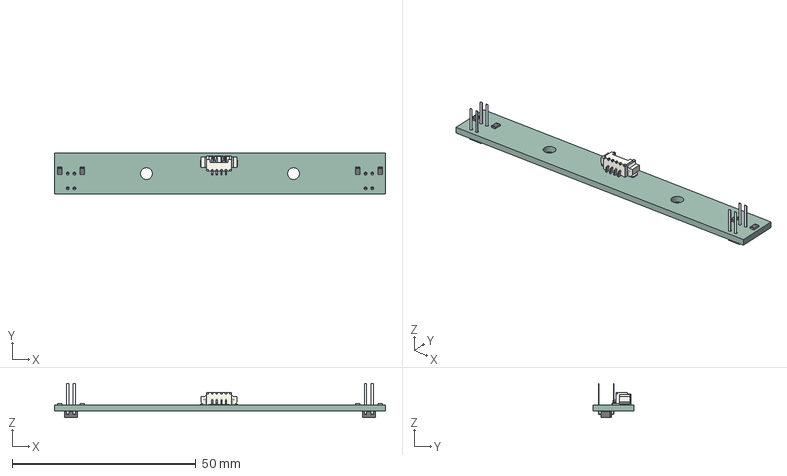
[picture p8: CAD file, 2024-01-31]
- PCB -/QRE MiniBoards/3D and Photos/QRE MiniBoards Board.step
90.0 x 11.0 x 9.25 mm
QRE MiniBoards PCB

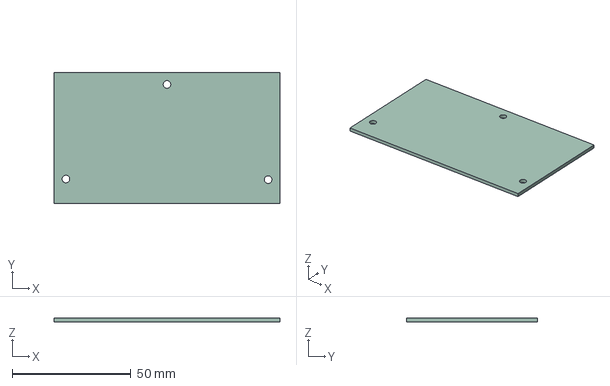
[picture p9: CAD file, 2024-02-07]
- PCB -/SUMEC SMD-V2/sumec.step
95.0 x 55.0 x 1.58 mm

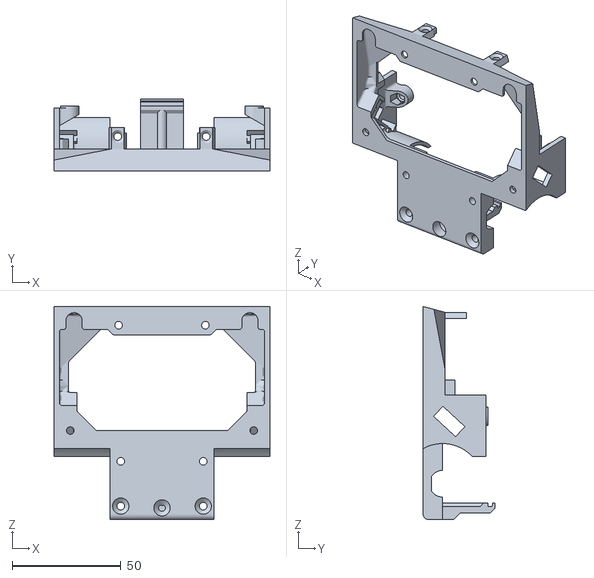
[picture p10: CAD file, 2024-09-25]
-3D-/body-motor_test_prototype.stl
99.5 x 33.1 x 98.2

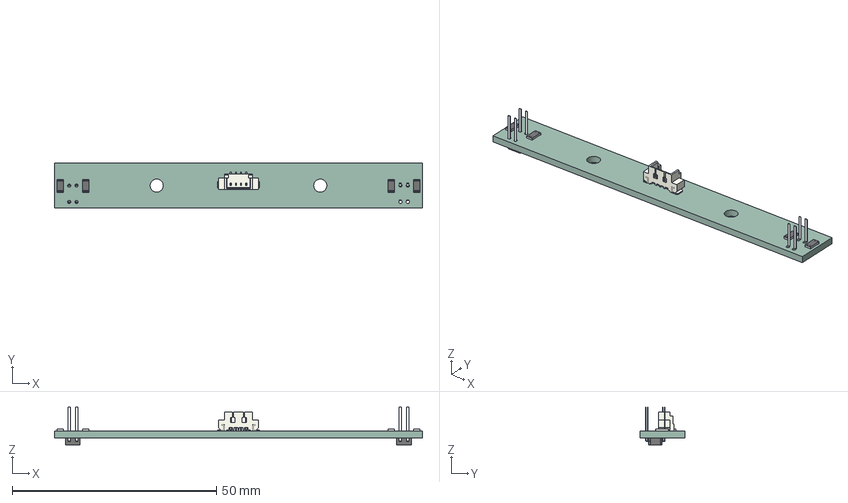
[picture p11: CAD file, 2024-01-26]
-3D-/el._parts/PCBs/QRE MiniBoards/QRE MiniBoards.step
90.0 x 11.0 x 9.25 mm
QRE MiniBoards PCB

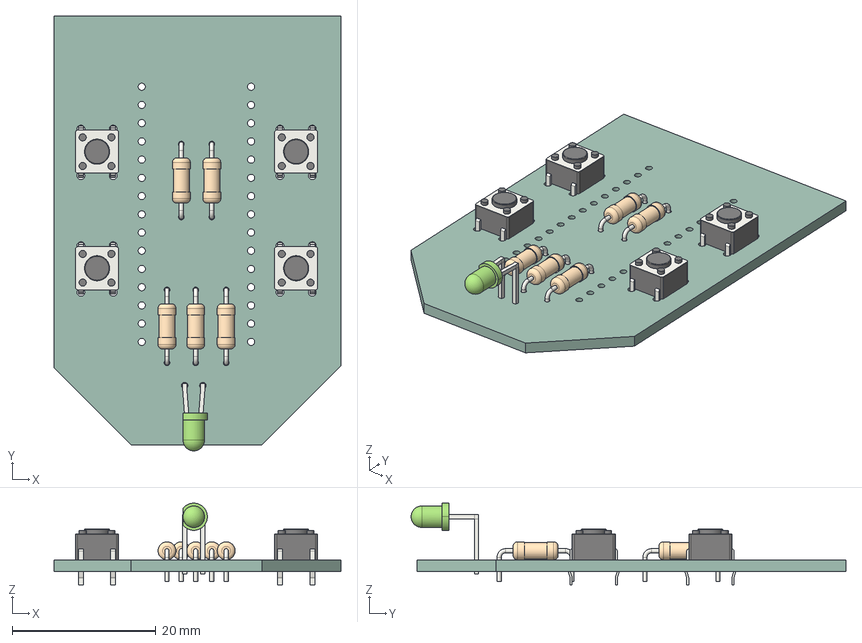
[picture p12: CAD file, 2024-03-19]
-3D-/el._parts/PCBs/RC5 Remote/RC-5 Remote Controler.step
40.0 x 60.6 x 11.4 mm
SW_PUSH_6mm x 4
R_Axial_DIN0207_L63mm_D25mm_P1016mm_Horizontal x 5
LED_D3.0mm_Horizontal_O3.81mm_Z6.0mm
RC-5 Remote Controler_PCB

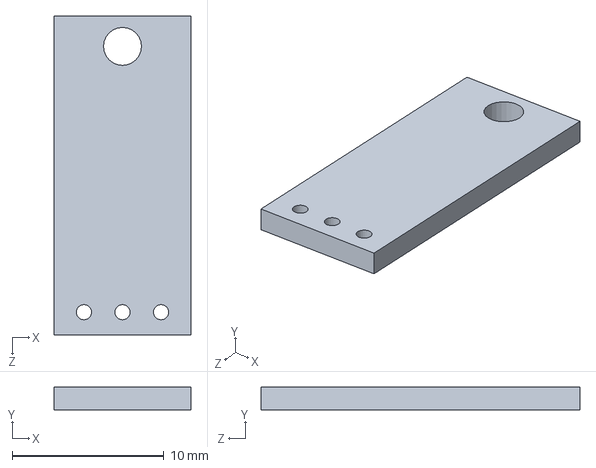
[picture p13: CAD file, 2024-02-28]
-3D-/el._parts/SensorSharpDigital/Base.SLDPRT
9.00 x 1.50 x 21.0 mm

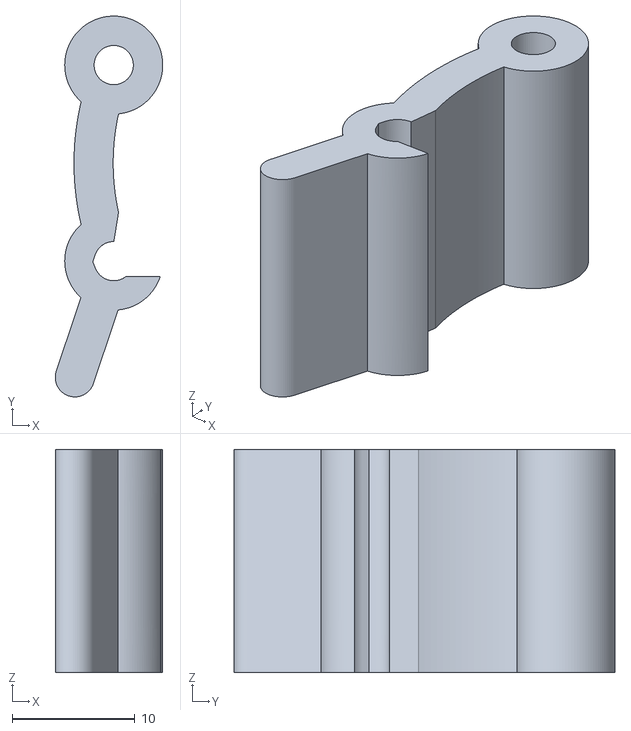
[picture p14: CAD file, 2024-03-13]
-3D-/sumec_box/Box - Latch.stl
8.77 x 31.1 x 18.2

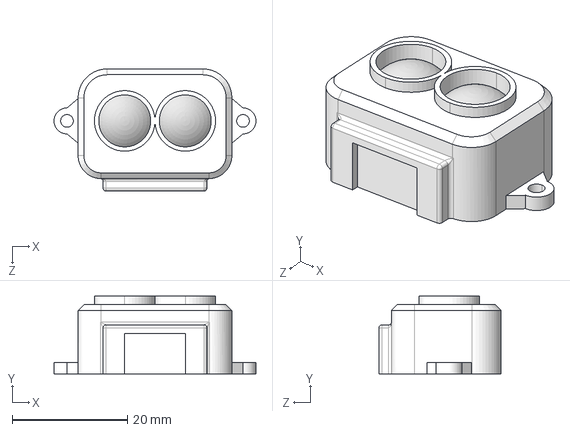
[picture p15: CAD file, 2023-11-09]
-DOCS-/SENSORS/TF Luna/3D/Sensor LUNA.STEP
35.0 x 13.5 x 21.2 mm

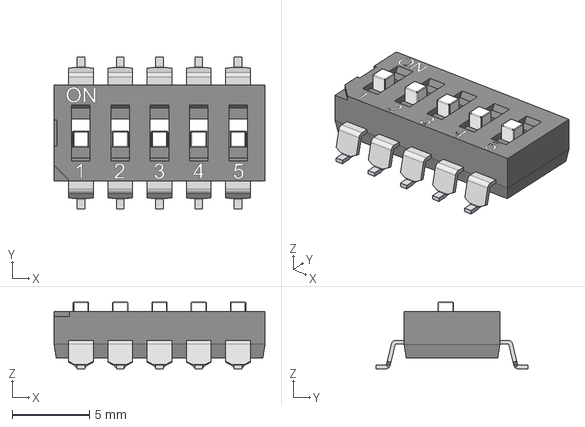
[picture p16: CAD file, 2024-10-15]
-PCB-/_libs/sumec_3d/SMD_DIP_SWITCH_5P.step
13.6 x 9.80 x 4.32 mm

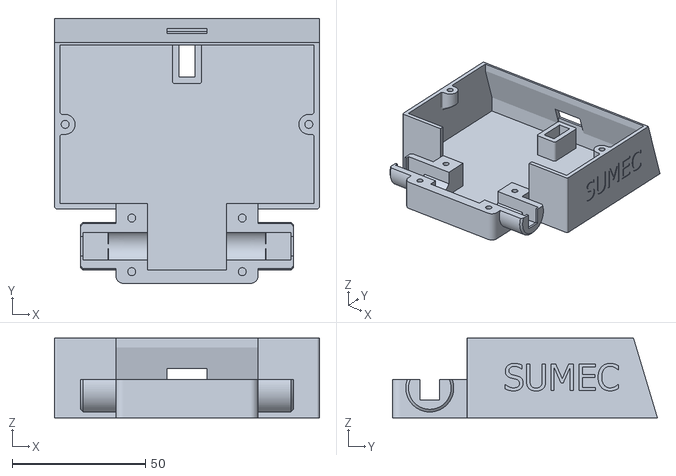
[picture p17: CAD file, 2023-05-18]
- 3D -/domov důchodců/sumec_2.2_body/Tělo.stl
99.5 x 99.5 x 30.0

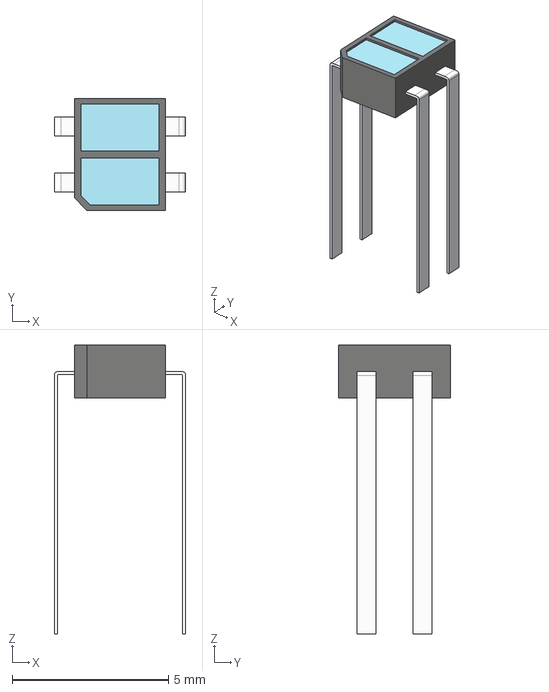
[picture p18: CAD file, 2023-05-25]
- PCB -/QRE MiniBoards/3D and Photos/QRE1113.stp
4.19 x 3.60 x 9.25 mm

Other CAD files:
-3D-/mech._parts/base_plate_v2.dwg
- 3D -/wip/Rozložení PCB bez laserů.dwg
-PCB-/_libs/sumec_3d/SPDT slide switch SS12D00.step
-3D-/el._parts/SensorSharpDigital/GP2Y0D810Z0F sharp.SLDPRT
- 3D -/_wip/new_plech.ipt
- 3D -/domov důchodců/pcb_1.0/7.4 V 500MaH Li pol.ipt
- 3D -/domov důchodců/pcb_1.0/CP_Radial_D4.0mm_P2.00mm.iam
- 3D -/domov důchodců/pcb_1.0/D_A-405_P2.54mm_Vertical_KathodeUp.iam
- 3D -/domov důchodců/pcb_1.0/H mustek.ipt
- 3D -/domov důchodců/pcb_1.0/PCB.ipt
- 3D -/domov důchodců/pcb_1.0/PinSocket_1x03_P2.54mm_Vertical.iam
- 3D -/domov důchodců/pcb_1.0/PinSocket_1x05_P2.54mm_Vertical.iam
- 3D -/domov důchodců/pcb_1.0/R_Axial_DIN0204_L3.6mm_D1.6mm_P1.90mm_Vertical.iam
- 3D -/domov důchodců/pcb_1.0/SOLID.ipt
- 3D -/domov důchodců/pcb_1.0/SOLID_1.ipt
- 3D -/domov důchodců/pcb_1.0/SOLID_2.ipt
- 3D -/domov důchodců/pcb_1.0/SOLID_3.ipt
- 3D -/domov důchodců/pcb_1.0/SOLID_4.ipt
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

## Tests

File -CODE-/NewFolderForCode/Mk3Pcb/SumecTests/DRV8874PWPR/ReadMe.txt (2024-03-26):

For this lib's test, see it's function directory
(it's the .ino file)

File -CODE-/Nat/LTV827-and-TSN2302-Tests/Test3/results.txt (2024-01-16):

START
New loop
2048
sda=0, XS1=0, XS2=0
Luna1: 	0
Luna2: 	0
===============	Result: ok

sda=1, XS1=0, XS2=0
Luna1: 	0
Luna2: 	0
===============	Result: ok

sda=0, XS1=1, XS2=0
Luna1: 	1
Luna2: 	0
===============	Result: NOT ok; sda

sda=0, XS1=0, XS2=1
Luna1: 	0
Luna2: 	0
===============	Result: ok

sda=1, XS1=1, XS2=0
Luna1: 	1
Luna2: 	1
===============	Result: NOT ok luna2

sda=1, XS1=0, XS2=1
Luna1: 	0
Luna2: 	1
===============	Result: ok

sda=0, XS1=1, XS2=1
Luna1: 	0
Luna2: 	0
===============	Result: ok

sda=1, XS1=1, XS2=1
Luna1: 	1
Luna2: 	1
===============	Result: ok

New loop------------------------------------------------------------------------
10548
sda=0, XS1=0, XS2=0
Luna1: 	0
Luna2: 	0
===============	Result: ok

sda=1, XS1=0, XS2=0
Luna1: 	0
Luna2: 	0
===============	Result: ok

sda=0, XS1=1, XS2=0
Luna1: 	1
Luna2: 	0
===============	Result: NOT ok; sda

sda=0, XS1=0, XS2=1
Luna1: 	0
Luna2: 	0
===============	Result: ok

sda=1, XS1=1, XS2=0
Luna1: 	1
Luna2: 	1
===============	Result: NOT ok; luna2

sda=1, XS1=0, XS2=1
Luna1: 	0
Luna2: 	1
===============	Result: ok

sda=0, XS1=1, XS2=1
Luna1: 	0
Luna2: 	0
===============	Result: ok

sda=1, XS1=1, XS2=1
Luna1: 	1
Luna2: 	1
===============	Result: ok

New loop-----------------------------------------------------------------
19048
sda=0, XS1=0, XS2=0
Luna1: 	0
Luna2: 	0
===============

sda=1, XS1=0, XS2=0
Luna1: 	0
Luna2: 	0
===============

sda=0, XS1=1, XS2=0
Luna1: 	1
Luna2: 	0
===============

sda=0, XS1=0, XS2=1
Luna1: 	0
Luna2: 	0
===============

sda=1, XS1=1, XS2=0
Luna1: 	1
Luna2: 	1
===============

sda=1, XS1=0, XS2=1
Luna1: 	0
Luna2: 	1
===============

sda=0, XS1=1, XS2=1
Luna1: 	0
Luna2: 	0
===============

sda=1, XS1=1, XS2=1
Luna1: 	1
Luna2: 	1
===============

New loop
27548
sda=0, XS1=0, XS2=0
Luna1: 	0
Luna2: 	0
===============

sda=1, XS1=0, XS2=0
Luna1: 	0
Luna2: 	0
===============

sda=0, XS1=1, XS2=0
Luna1: 	1
Luna2: 	0
===============

sda=0, XS1=0, XS2=1
Luna1: 	0
Luna2: 	0
===============

sda=1, XS1=1, XS2=0
Luna1: 	1
Luna2: 	0
===============

sda=1, XS1=0, XS2=1
Luna1: 	0
Luna2: 	1
===============

sda=0, XS1=1, XS2=1
Luna1: 	0
Luna2: 	0
===============

sda=1, XS1=1, XS2=1
Luna1: 	1
Luna2: 	1
===============

New loop
36048
sda=0, XS1=0, XS2=0
Luna1: 	0
Luna2: 	0
===============

sda=1, XS1=0, XS2=0
Luna1: 	0
Luna2: 	0
===============

sda=0, XS1=1, XS2=0
Luna1: 	1
Luna2: 	0
===============

sda=0, XS1=0, XS2=1
Luna1: 	0
Luna2: 	0
===============

sda=1, XS1=1, XS2=0
Luna1: 	1
Luna2: 	0
===============

sda=1, XS1=0, XS2=1
Luna1: 	0
Luna2: 	1
===============

sda=0, XS1=1, XS2=1
Luna1: 	0
Luna2: 	0
===============

sda=1, XS1=1, XS2=1
Luna1: 	1
Luna2: 	1
===============

New loop
44548
sda=0, XS1=0, XS2=0
Luna1: 	0
Luna2: 	0
===============

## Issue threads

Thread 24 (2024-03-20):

DRV8874 Driver has internal current protection, this issue will be fixed in smd-V3

bismarx-v1, 2024-03-20:
https://www.ti.com/lit/ds/symlink/drv8874.pdf?ts=1708431513344&ref_url=https%253A%252F%252Fwww.google.com%252F

Its better to make a breakout board for such driver, making the breakout board is our sub-issue

bismarx-v1, 2024-10-02:
tested on a breakout board, fixed

Closed 2024-10-02.

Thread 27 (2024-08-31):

a few kicad files crash instantly when opeing

NataniSi, 2024-08-31:
A few kicad files crash instantly when opeing

Occurs when opening through the ".kicad_pro" file or when opening files individually.
Affected files:

[-PCB-/_archive_old/SUMEC_SMD-V2/MECHANICS.kicad_sch](https://github.com/bismarx-v1/Sumec-MiniSumo/blob/a65e63b65f2ede6e8036a4a3e1dbe55981a46eda/-PCB-/_archive_old/SUMEC_SMD-V2/MECHANICS.kicad_sch)
[-PCB-/_archive_old/SUMEC_SMD-V2/POWER SUPPLY.kicad_sch](https://github.com/bismarx-v1/Sumec-MiniSumo/blob/a65e63b65f2ede6e8036a4a3e1dbe55981a46eda/-PCB-/_archive_old/SUMEC_SMD-V2/POWER%20SUPPLY.kicad_sch)
[-PCB-/_archive_old/SUMEC_SMD-V2/SENSORS.kicad_sch](https://github.com/bismarx-v1/Sumec-MiniSumo/blob/a65e63b65f2ede6e8036a4a3e1dbe55981a46eda/-PCB-/_archive_old/SUMEC_SMD-V2/SENSORS.kicad_sch)
[-PCB-/SUMEC_MK_IV/MECHANICS.kicad_sch](https://github.com/bismarx-v1/Sumec-MiniSumo/blob/a65e63b65f2ede6e8036a4a3e1dbe55981a46eda/-PCB-/SUMEC_MK_IV/MECHANICS.kicad_sch)
[-PCB-/SUMEC_MK_IV/POWER_SUPPLY.kicad_sch](https://github.com/bismarx-v1/Sumec-MiniSumo/blob/a65e63b65f2ede6e8036a4a3e1dbe55981a46eda/-PCB-/SUMEC_MK_IV/POWER_SUPPLY.kicad_sch)
[-PCB-/SUMEC_MK_IV/SENSORS.kicad_sch](https://github.com/bismarx-v1/Sumec-MiniSumo/blob/a65e63b65f2ede6e8036a4a3e1dbe55981a46eda/-PCB-/SUMEC_MK_IV/SENSORS.kicad_sch)

bismarx-v1, 2024-09-01:
Maybe gitignore affects this? Ill change gitignore let me know if its going to fix it.

bismarx-v1, 2024-10-02:
I think this one is fixed

Closed 2024-10-02.

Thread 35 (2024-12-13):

useless suff in docs, missing needed stuff

NataniSi, 2024-12-13:
no main in the code folder is a docs file called "FULL SCHEMATIC PDF.pdf". my issues are that it ahs spaces in the name, and that's wrong. a bigger issue i have is that there is no pcb version number. glad there is the big logo though. we figured out it's probably the mk3 pcb, but each page has a table in the bottom right corner and the file has a name, yet no version number to be found. :3

bismarx-v1, 2024-12-13:
fixed

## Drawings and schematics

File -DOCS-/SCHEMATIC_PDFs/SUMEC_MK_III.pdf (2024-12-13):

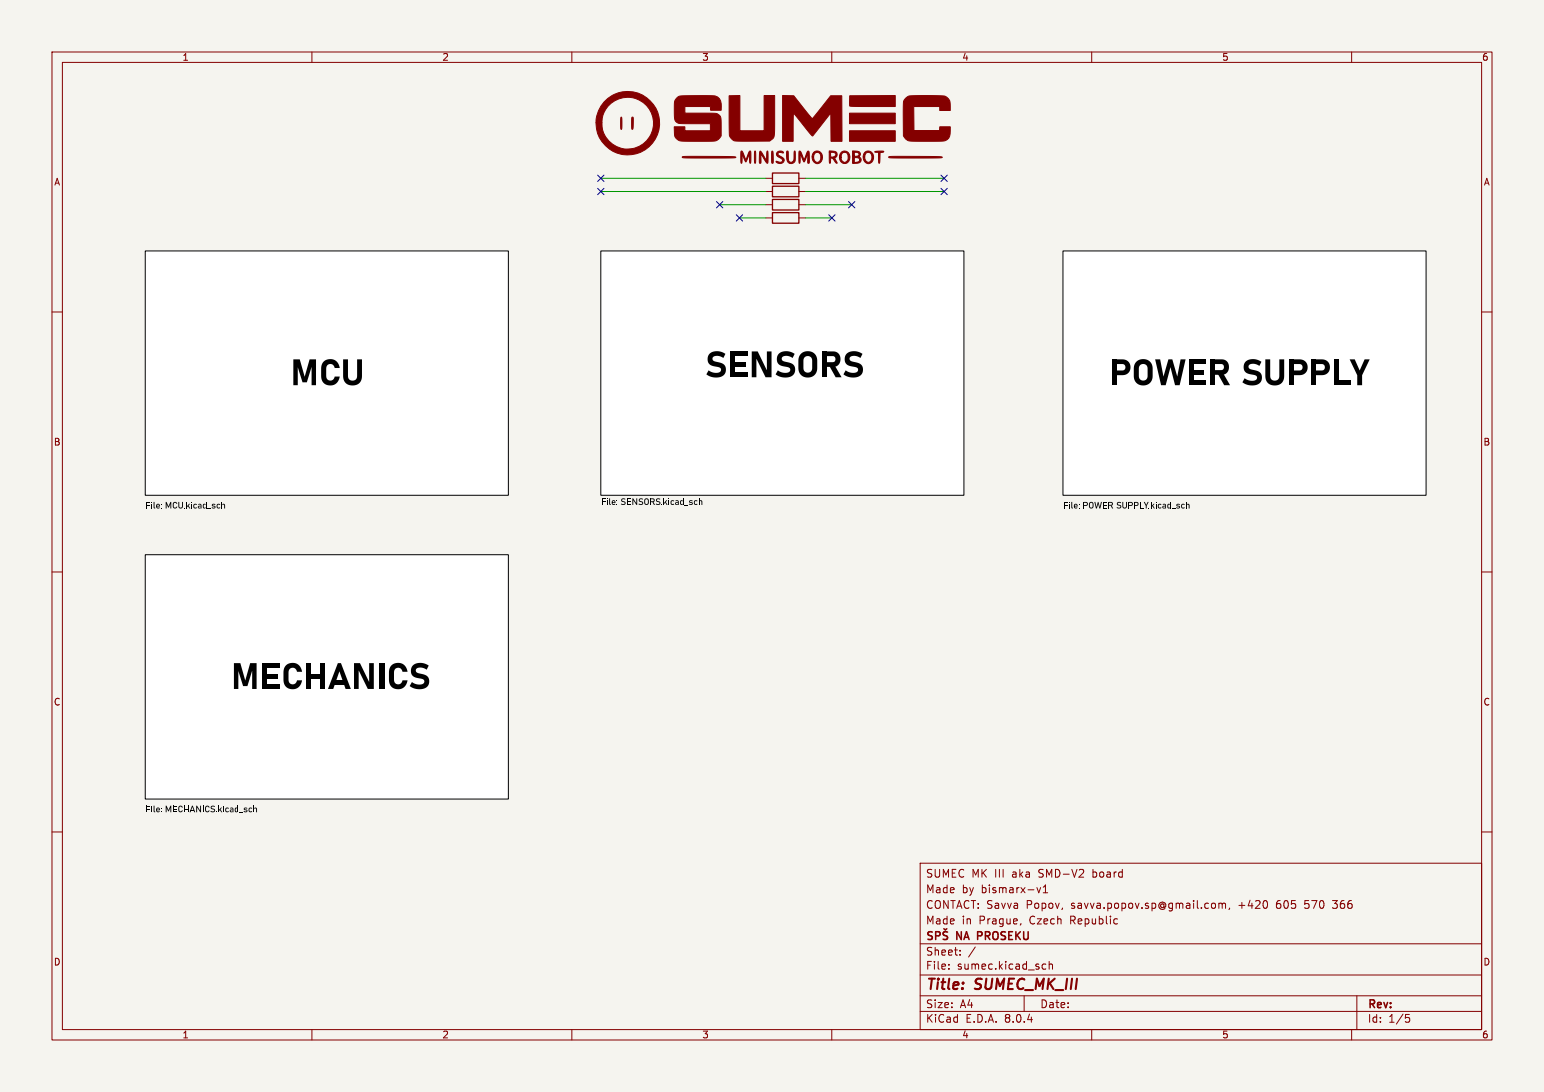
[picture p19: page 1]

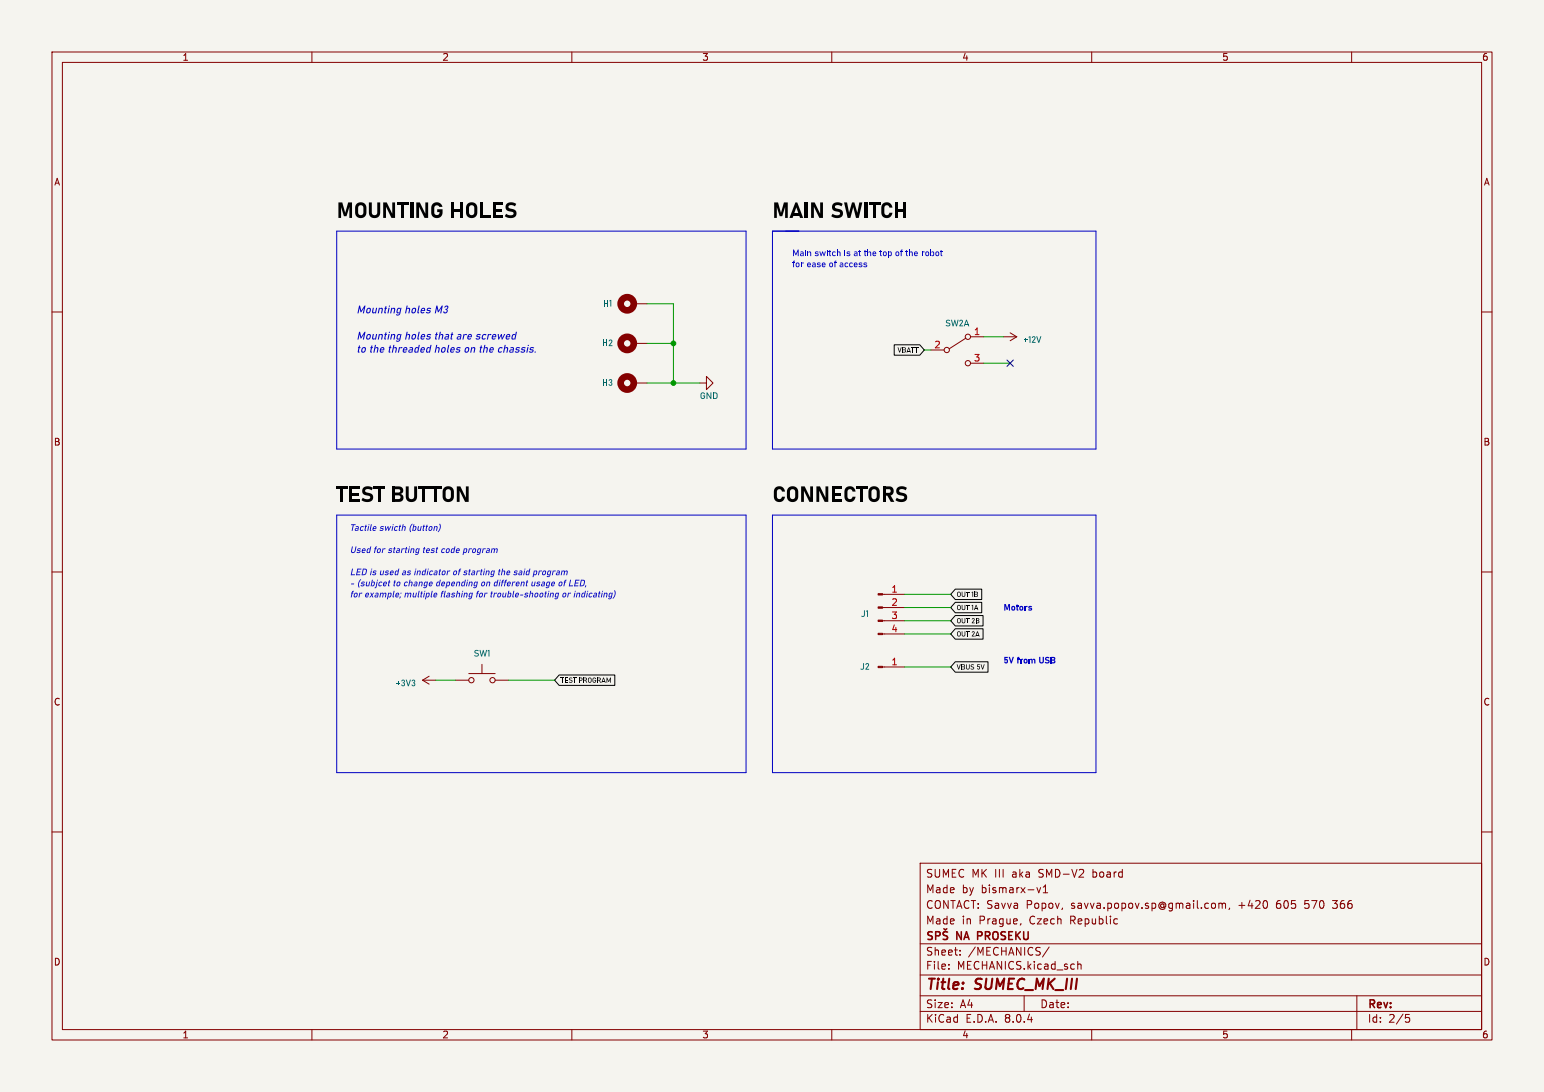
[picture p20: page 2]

Main switch is at the top of the robot

Mounting holes M3 Mounting holes that are screwed

Tactile swicth (button) Used for starting test code program

LED is used as indicator of starting the said program
- (subjcet to change depending on different usage of LED,
for example; multiple flashing for trouble-shooting or indicating)

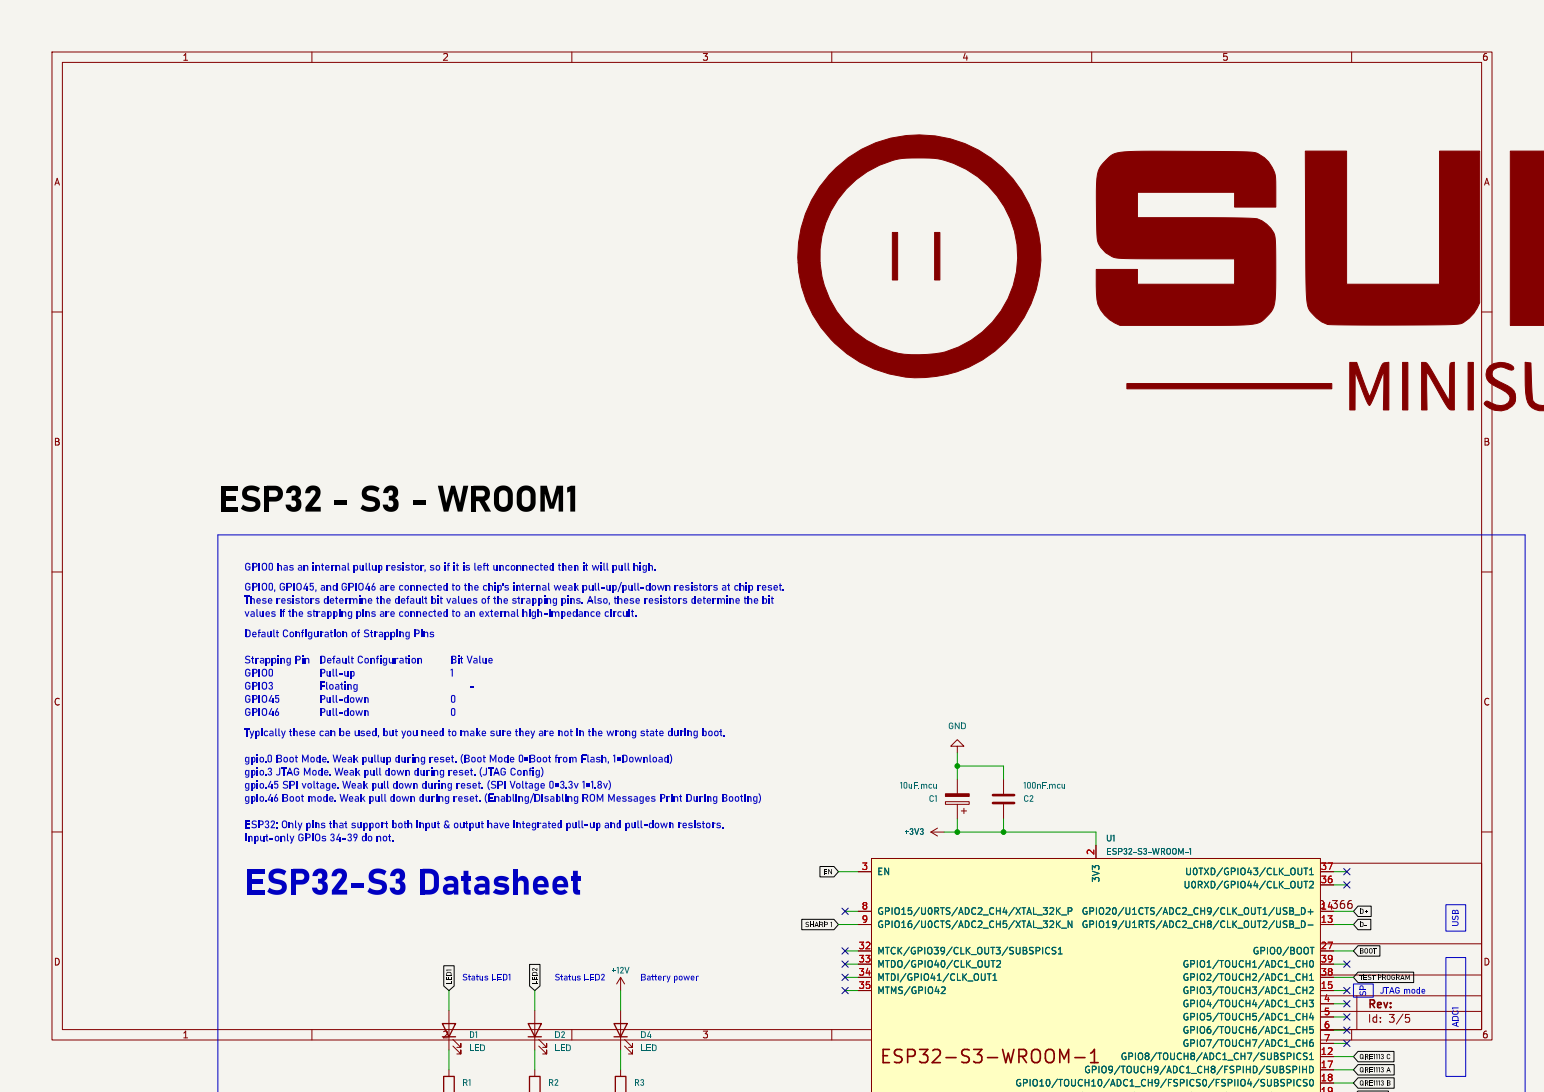
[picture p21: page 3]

Typically these can be used, but you need to make sure they are not in the wrong state during boot. gpio.0Boot Mode.Weakpullup during reset. (Boot Mode 0=Boot from Flash, 1=Download)

gpio.3 JTAGMode.Weakpull down during reset. (JTAGConfig)
gpio.45 SPI voltage. Weakpull down during reset. (SPIVoltage 0=3.3v1=1.8v)

ESP32:Only pins that support both input & output have integrated pull-up and pull-down resistors.
Input-only GPIOs34-39 do not. ESP32-S3Datasheet

2 GPIO12/TOUCH12/ADC2_CH1/FSPICLK/FSPIIO6/SUBSPICLK 20 GPIO13/TOUCH13/ADC2_CH2/FSPIQ/FSPIIO7/SUBSPIQ 21 GPIO14/TOUCH14/ADC2_CH3/FSPIWP/FSPIDQS/SUBSPIWP 22 GPIO21 23 GPIO47/SPICLK_P/SUBSPICLK_P_DIFF 24 GPIO48/SPICLK_N/SUBSPICLK_N_DIFF 25 GPIO45 26 GPIO0/BOOT 27 SPIIO6/GPIO35/FSPID/SUBSPID 28 SPIIO7/GPIO36/FSPICLK/SUBSPICLK 29 EN 3 SPIDQS/GPIO37/FSPIQ/SUBSPIQ 30 GPIO38/FSPIWP/SUBSPIWP 31 MTCK/GPIO39/CLK_OUT3/SUBSPICS1 32 MTDO/GPIO40/CLK_OUT2 33 MTDI/GPIO41/CLK_OUT1 34 MTMS/GPIO42 35 U0RXD/GPIO44/CLK_OUT2 36 U0TXD/GPIO43/CLK_OUT1 37 GPIO2/TOUCH2/ADC1_CH1 38 GPIO1/TOUCH1/ADC1_CH0 39 GPIO4/TOUCH4/ADC1_CH3 4 GPIO5/TOUCH5/ADC1_CH4 5 GPIO6/TOUCH6/ADC1_CH5 6 GPIO7/TOUCH7/ADC1_CH6 7 GPIO15/U0RTS/ADC2_CH4/XTAL_32K_P 8 GPIO16/U0CTS/ADC2_CH5/XTAL_32K_N 9 U1ESP32-S3-WROOM-1 C11

2 GPIO12/TOUCH12/ADC2_CH1/FSPICLK/FSPIIO6/SUBSPICLK 20 GPIO13/TOUCH13/ADC2_CH2/FSPIQ/FSPIIO7/SUBSPIQ 21 GPIO14/TOUCH14/ADC2_CH3/FSPIWP/FSPIDQS/SUBSPIWP 22 GPIO21 23 GPIO47/SPICLK_P/SUBSPICLK_P_DIFF 24 GPIO48/SPICLK_N/SUBSPICLK_N_DIFF 25 GPIO45 26 GPIO0/BOOT 27 SPIIO6/GPIO35/FSPID/SUBSPID 28 SPIIO7/GPIO36/FSPICLK/SUBSPICLK 29 EN 3 SPIDQS/GPIO37/FSPIQ/SUBSPIQ 30 GPIO38/FSPIWP/SUBSPIWP 31 MTCK/GPIO39/CLK_OUT3/SUBSPICS1 32 MTDO/GPIO40/CLK_OUT2 33 MTDI/GPIO41/CLK_OUT1 34 MTMS/GPIO42 35 U0RXD/GPIO44/CLK_OUT2 36 U0TXD/GPIO43/CLK_OUT1 37 GPIO2/TOUCH2/ADC1_CH1 38 GPIO1/TOUCH1/ADC1_CH0 39 GPIO4/TOUCH4/ADC1_CH3 4 GPIO5/TOUCH5/ADC1_CH4 5 GPIO6/TOUCH6/ADC1_CH5 6 GPIO7/TOUCH7/ADC1_CH6 7 GPIO15/U0RTS/ADC2_CH4/XTAL_32K_P 8 GPIO16/U0CTS/ADC2_CH5/XTAL_32K_N 9 C3

1 GPIO17/U1TXD/ADC2_CH6 10 GPIO18/U1RXD/ADC2_CH7/CLK_OUT3 11 GPIO8/TOUCH8/ADC1_CH7/SUBSPICS1 12 GPIO19/U1RTS/ADC2_CH8/CLK_OUT2/USB_D- 13 GPIO20/U1CTS/ADC2_CH9/CLK_OUT1/USB_D+ 14 GPIO3/TOUCH3/ADC1_CH2 15 GPIO46 16 GPIO9/TOUCH9/ADC1_CH8/FSPIHD/SUBSPIHD 17 GPIO10/TOUCH10/ADC1_CH9/FSPICS0/FSPIIO4/SUBSPICS0 18 GPIO11/TOUCH11/ADC2_CH0/FSPID/FSPIIO5/SUBSPID 19 3V3

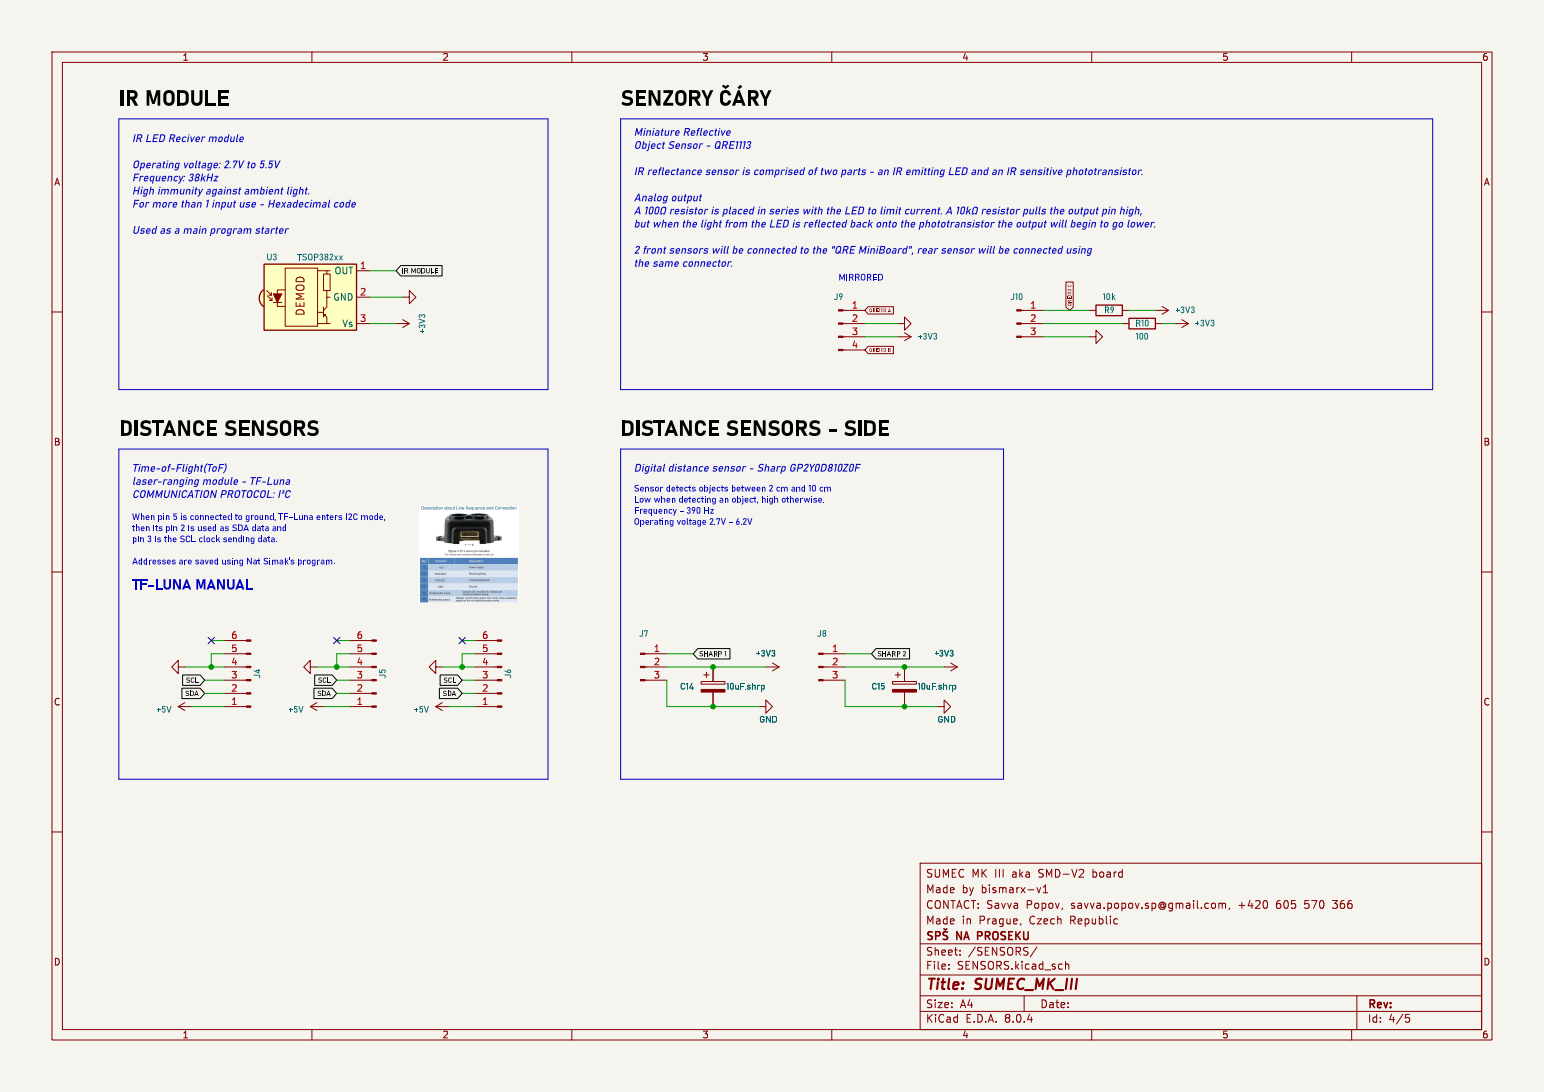
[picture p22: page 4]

the same connector. SENZORYþÿÁRY

IR LED Reciver module Operating voltage: 2.7Vto 5.5V

QRE1113A QRE1113B Miniature Reflective Object Sensor - QRE1113

IR reflectance sensor is comprised of two parts - an IR emitting LED and an IR sensitive phototransistor.
J9 GND

Analog output A þÿ100© resistor is placed in series with the LED to limit current. A þÿ10k© resistor pulls the output pin high, but when the light from the LED is reflected back onto the phototransistor the output will begin to go lower. 2 front sensors will be connected to the "QREMiniBoard", rear sensor will be connected using

Low when detecting an object, high otherwise. Frequency - 390 Hz Operating voltage 2.7V- 6.2V DISTANCESENSORS

Time-of-Flight(ToF)
laser-ranging module - TF-Luna COMMUNICATIONPROTOCOL:þÿI²C When pin 5 is connected to ground, TF-Luna enters I2Cmode,

Sensor detects objects between 2 cm and 10cm

then its pin 2 is used as SDAdata and
pin 3 is the SCLclock sending data. Addresses are saved using Nat Simak's program. TF-LUNAMANUAL

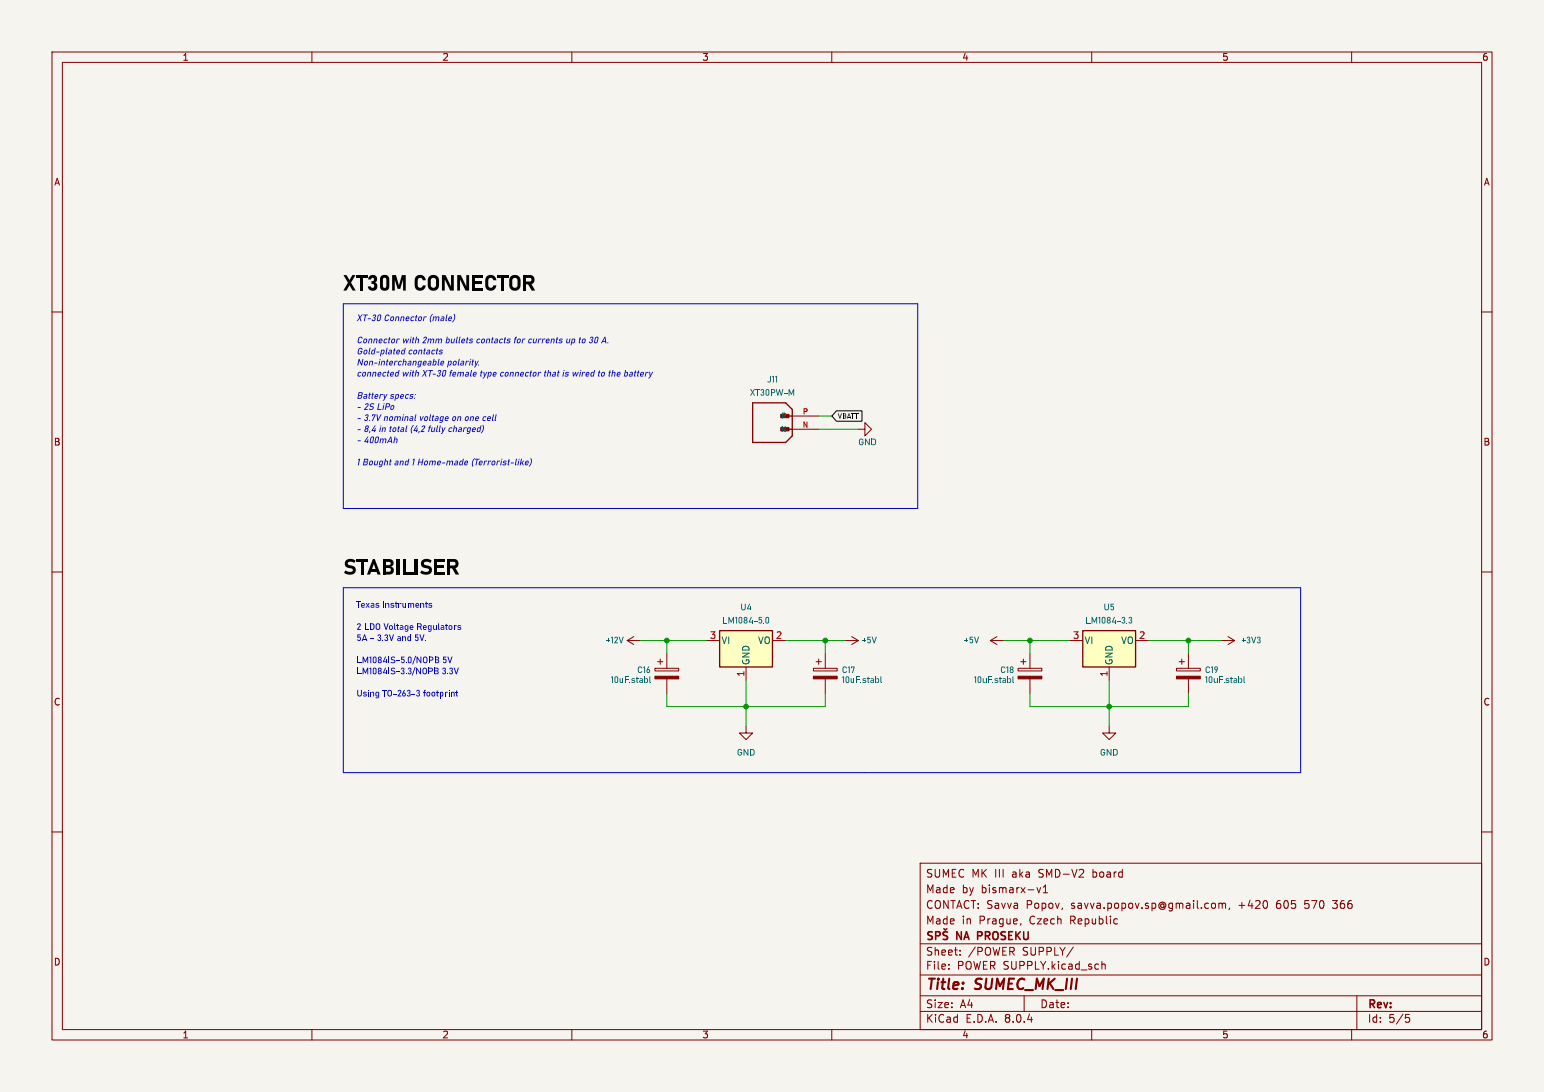
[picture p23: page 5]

XT-30 Connector (male) Connector with 2mm bullets contacts for currents up to 30 A. Gold-plated contacts Non-interchangeable polarity. connected with XT-30 female type connector that is wired to the battery

VBATT TexasInstruments 2 LDOVoltage Regulators 5A - 3.3Vand 5V. LM1084IS-5.0/NOPB5V
- 3.7Vnominal voltage on one cell - 8,4 in total (4,2 fully charged)

1Bought and 1Home-made (Terrorist-like)

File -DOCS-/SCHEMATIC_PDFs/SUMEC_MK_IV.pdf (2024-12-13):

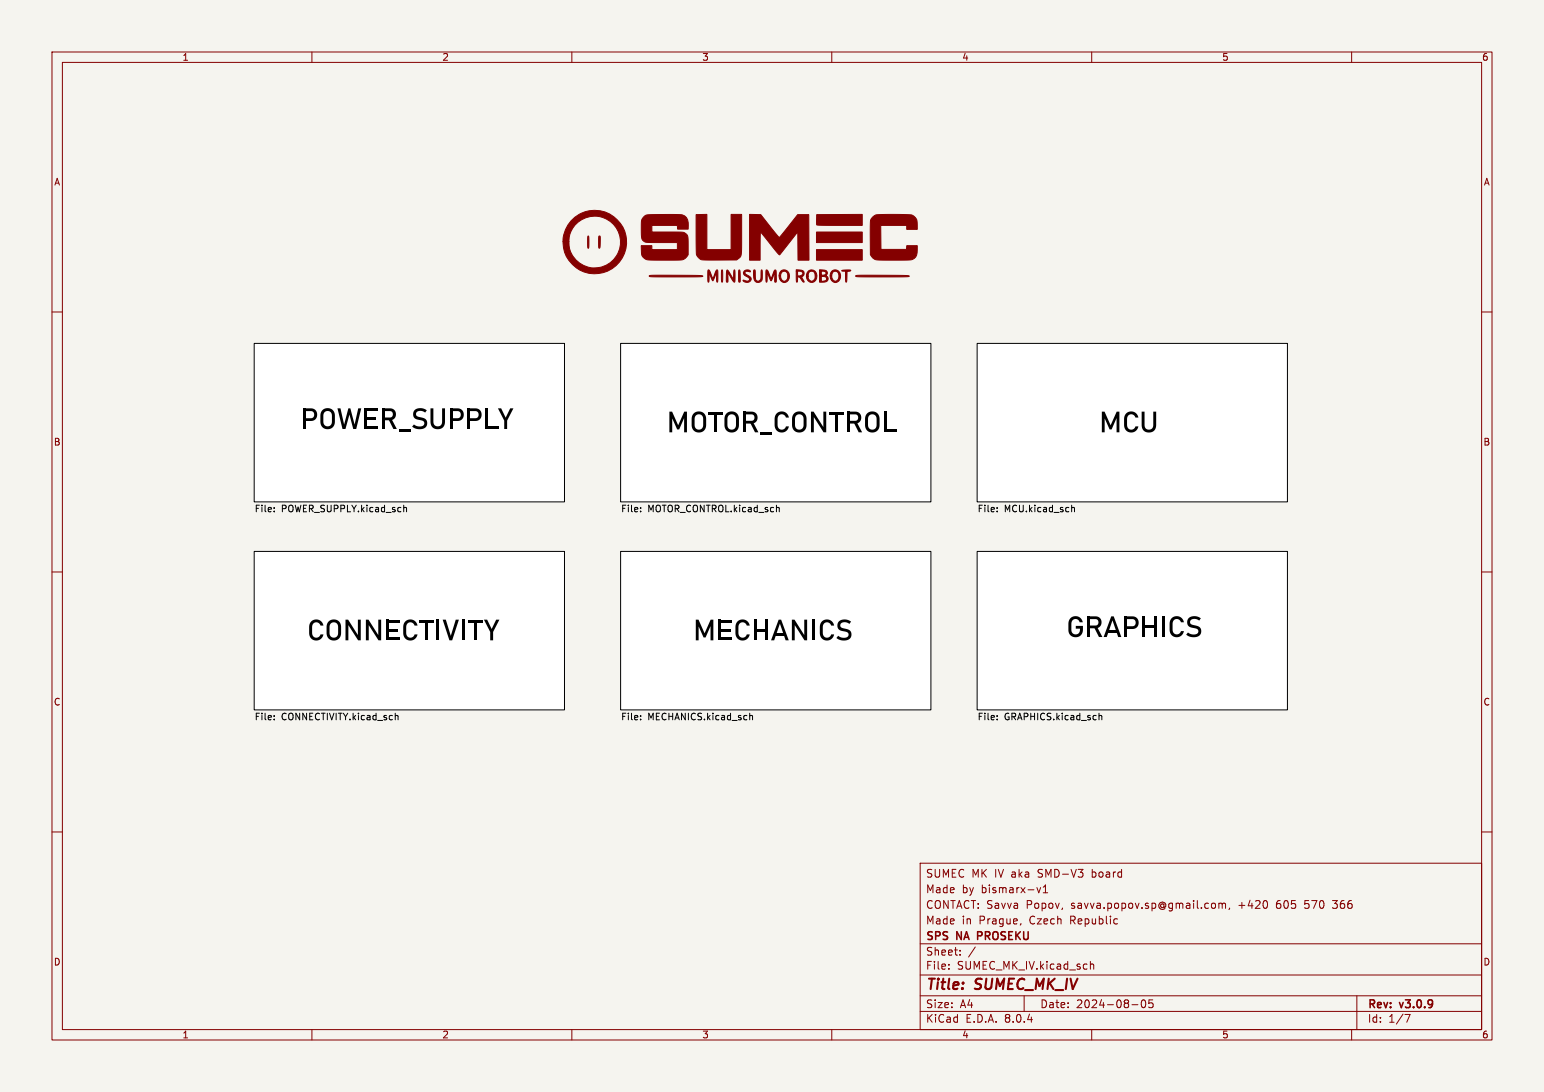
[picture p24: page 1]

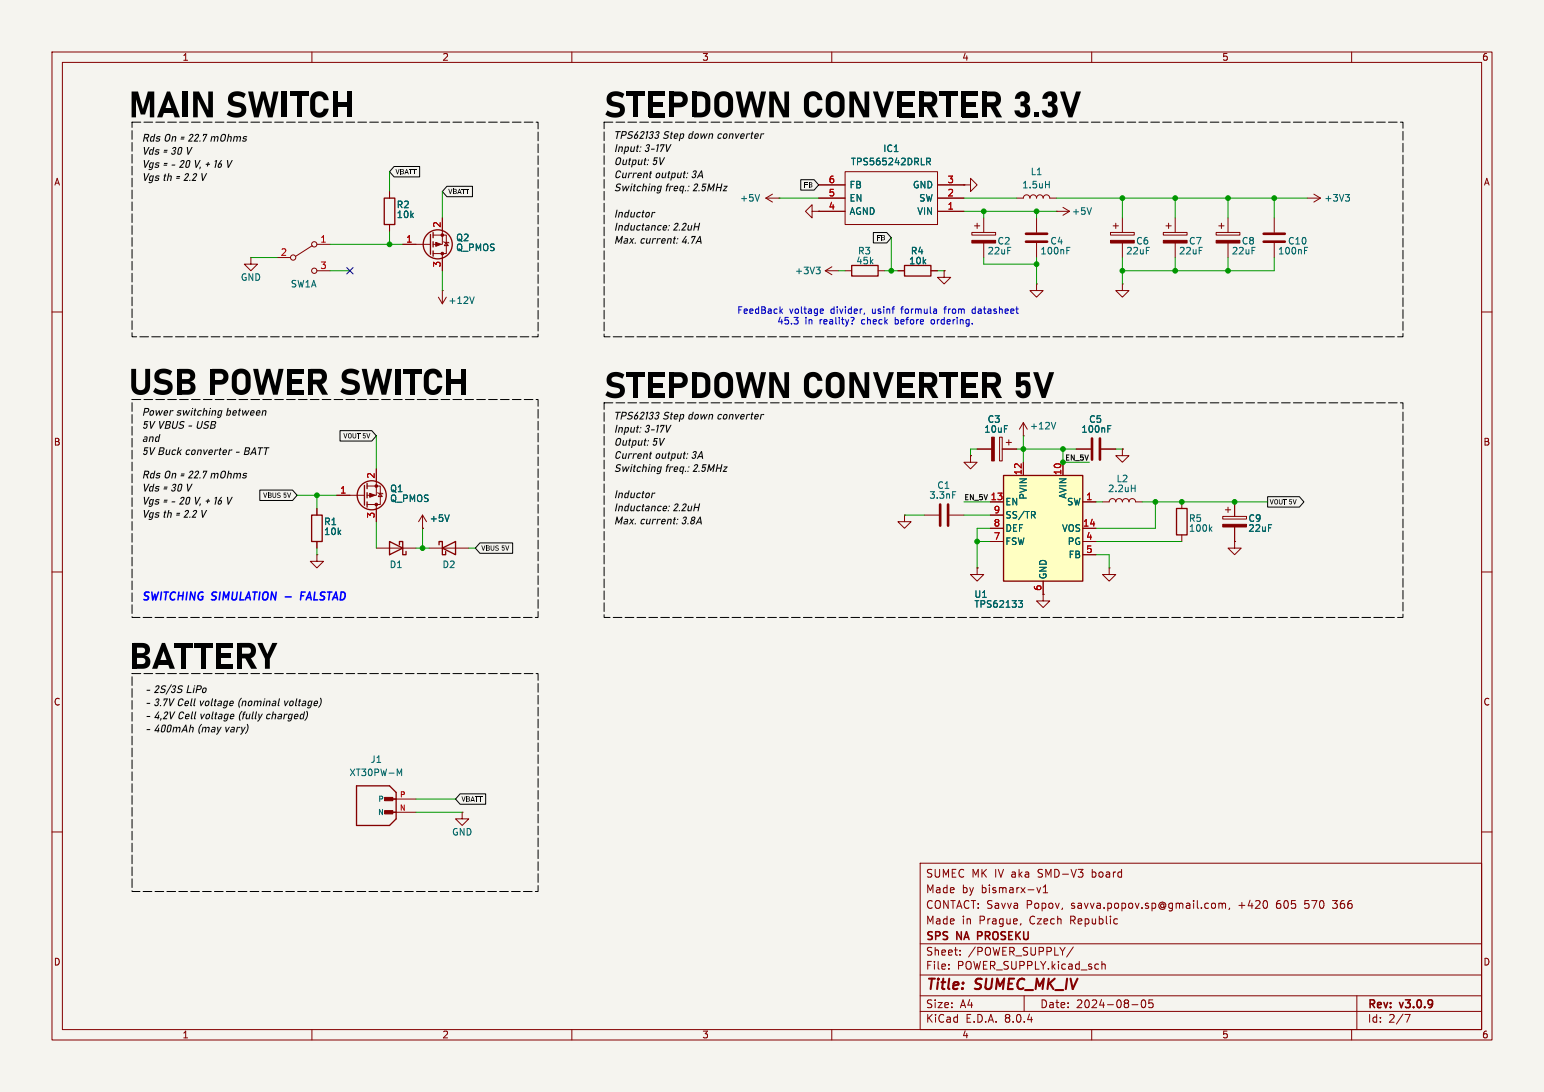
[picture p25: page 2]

Inductance: 2.2uH Max. current: 3.8A MAINSWITCH

Input: 3-17V Output: 5V Current output: 3A

6 FSW 7 DEF 8 SS/TR 9 U1 TPS62133 R4

6 FSW 7 DEF 8 SS/TR 9 R4

SWITCHING SIMULATION - FALSTAD (https://www.youtube.com/watch?v=lVDUcCuKls0) USBPOWERSWITCH Power switching between

TPS62133Step down converter

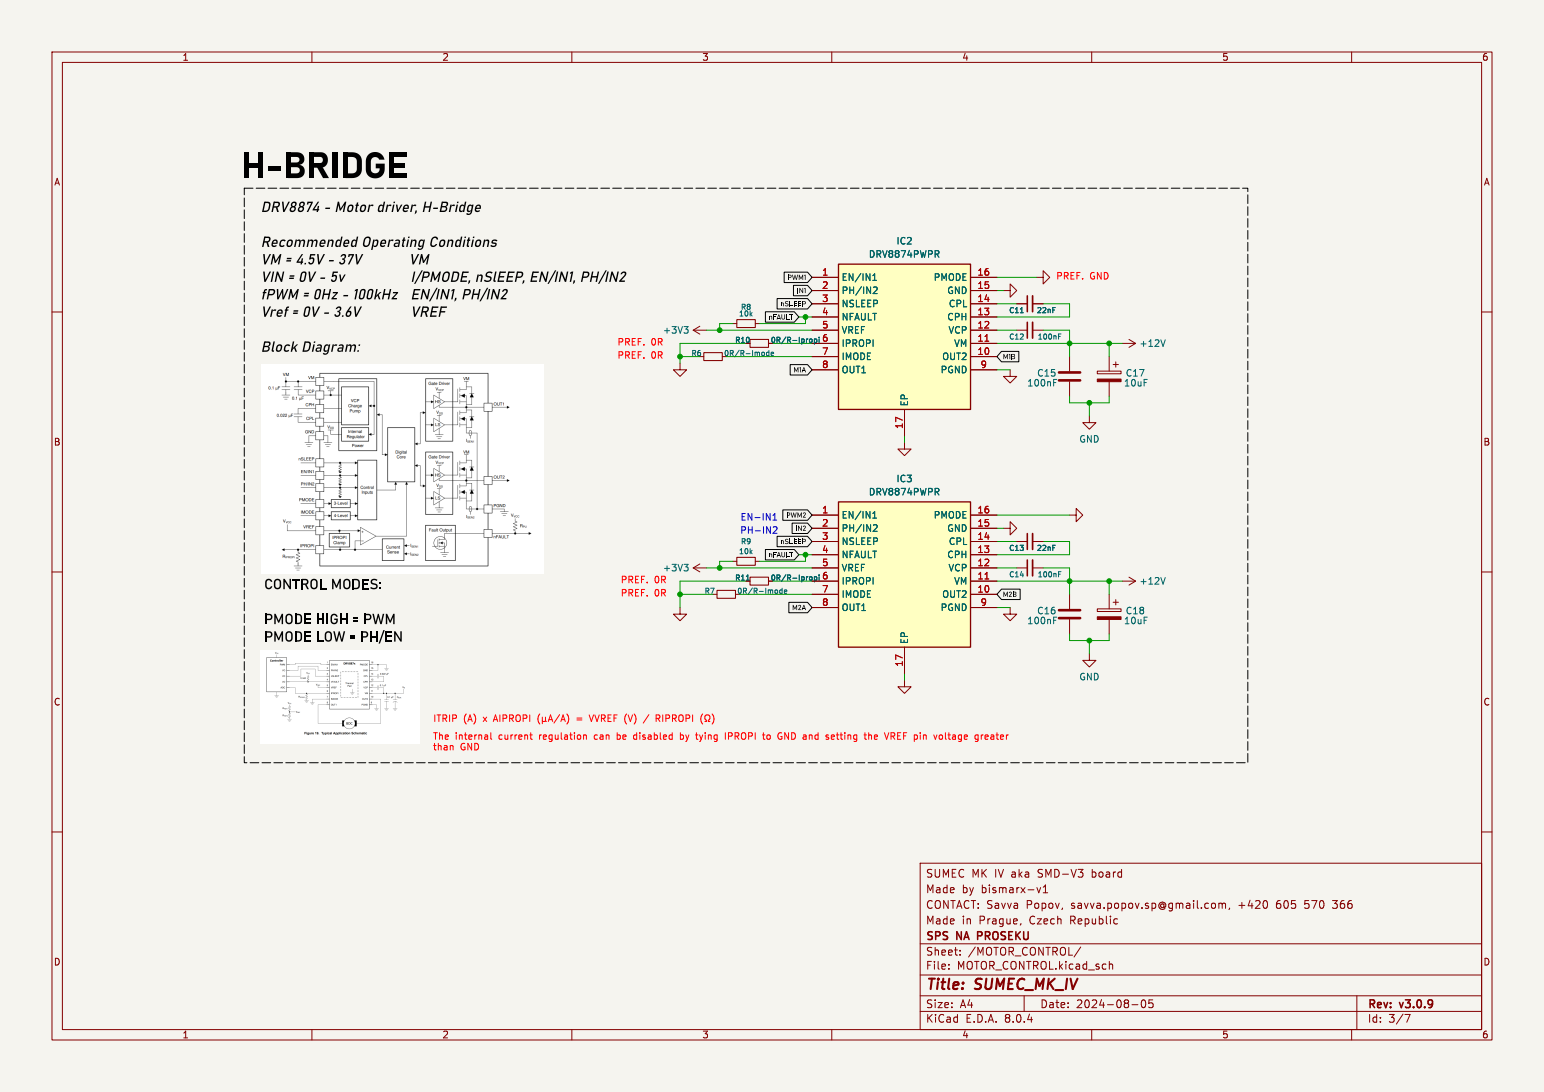
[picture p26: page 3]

ITRIP (A) x AIPROPI þÿ(¼A/A) = VVREF (V) / RIPROPI þÿ(!&)EN-IN1 CONTROLMODES:

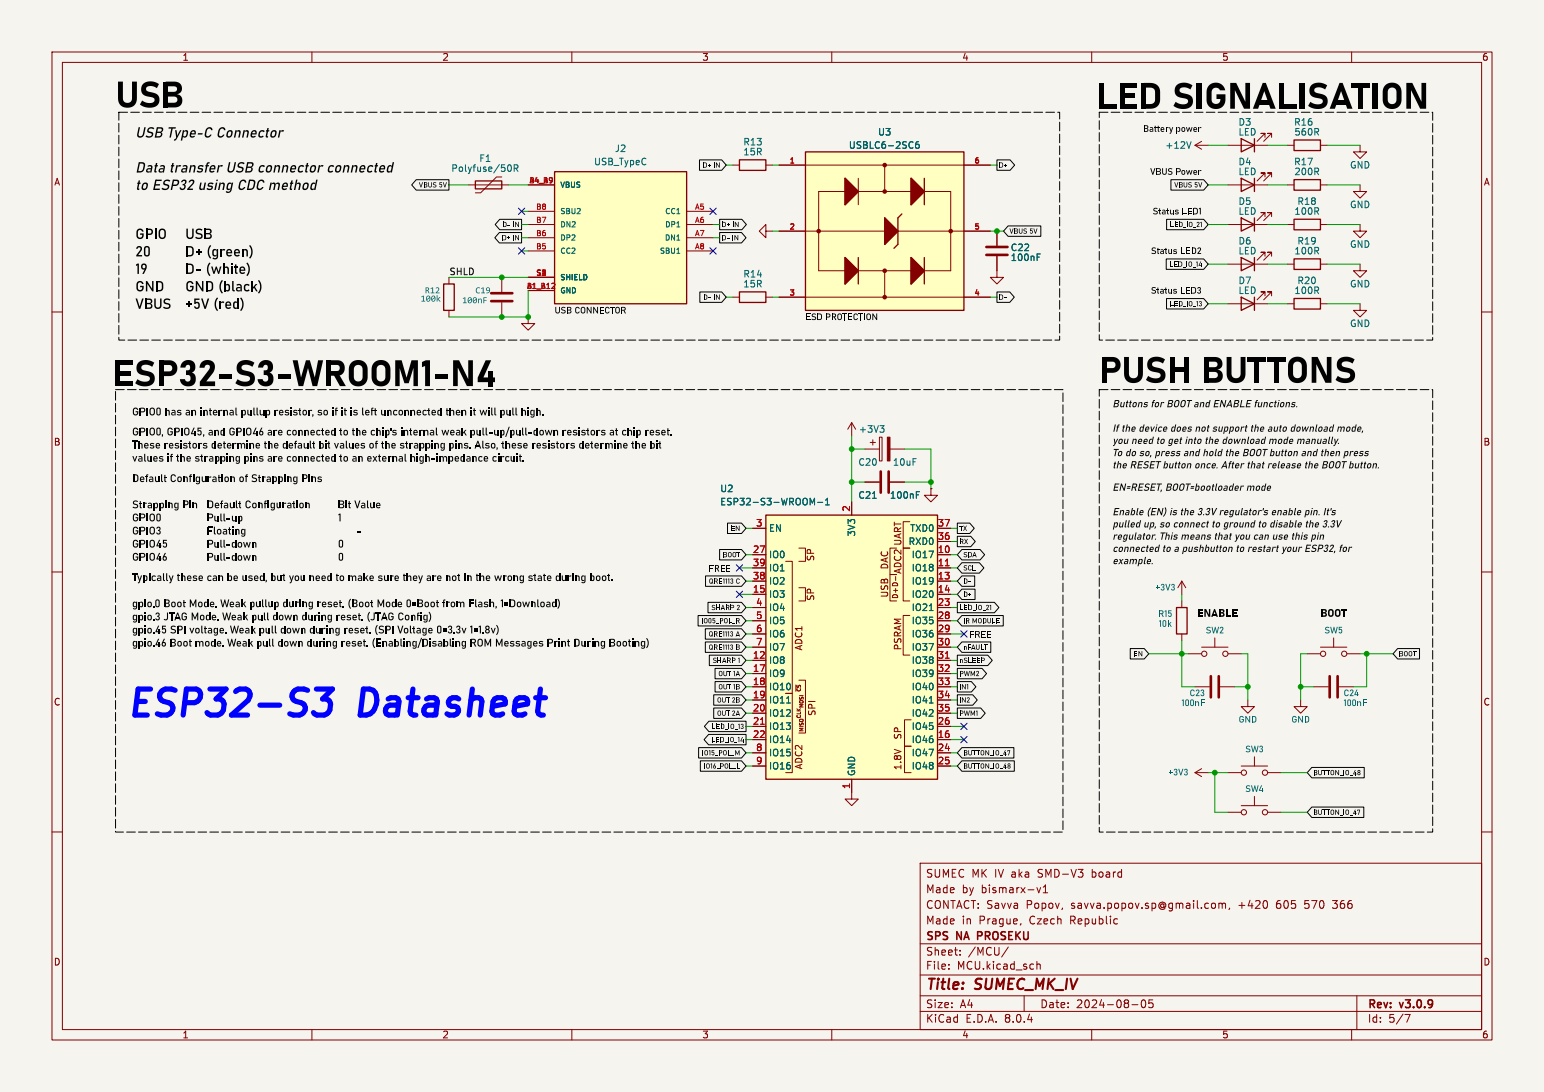
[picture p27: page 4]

Data transfer USBconnector connected
to ESP32using CDCmethod

VBUSPower EN=RESET,BOOT=bootloadermode Enable (EN) is the 3.3Vregulator's enable pin. It's pulled up, so connect to ground to disable the 3.3V

If the device does not support the auto download mode, you need to get into the download mode manually. Todo so, press and hold the BOOTbutton and then press

regulator. This means that you can use this pin
connected to a pushbutton to restart your ESP32,for example.

Typically these can be used, but you need to make sure they are not in the wrong state during boot. gpio.0Boot Mode.Weakpullup during reset. (Boot Mode 0=Boot from Flash, 1=Download)

gpio.3 JTAGMode.Weakpull down during reset. (JTAGConfig)
gpio.45 SPI voltage. Weakpull down during reset. (SPIVoltage 0=3.3v1=1.8v)

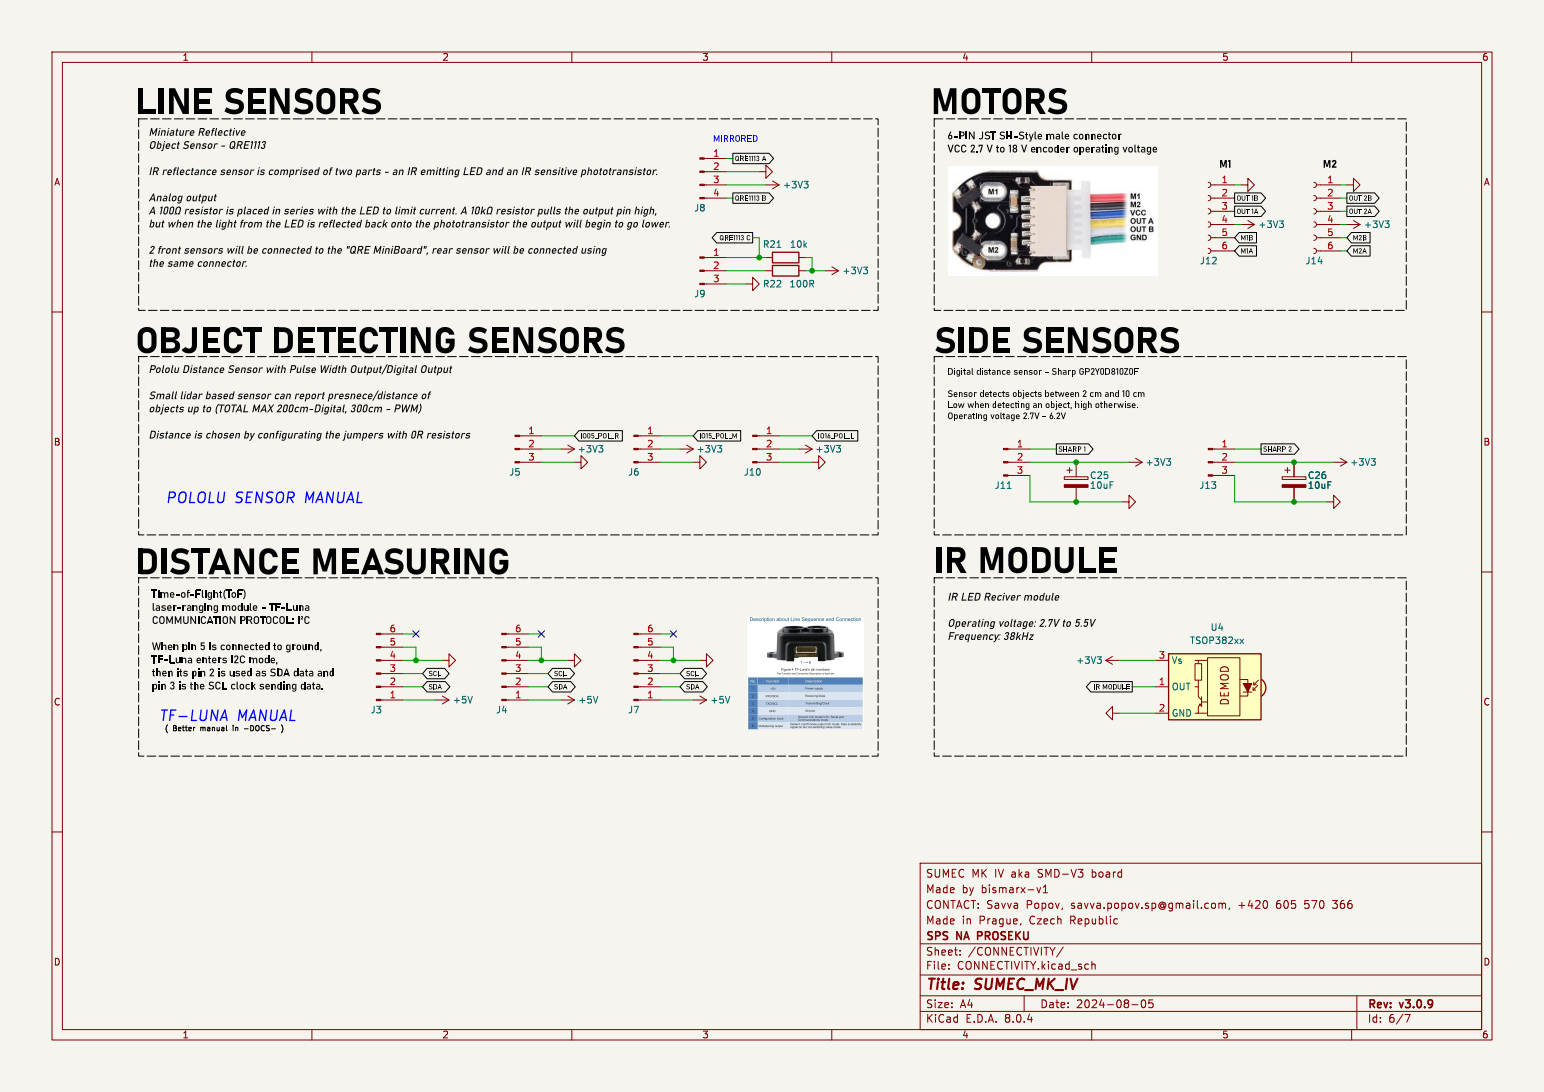
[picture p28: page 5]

pin 3 is the SCLclock sending data. Miniature Reflective Object Sensor - QRE1113

6-PIN JSTSH-Style male connector VCC2.7V to 18V encoder operating voltage

IR reflectance sensor is comprised of two parts - an IR emitting LED and an IR sensitive phototransistor.

the same connector. OBJECTDETECTINGSENSORS

Analog output A þÿ100© resistor is placed in series with the LED to limit current. A þÿ10k© resistor pulls the output pin high, but when the light from the LED is reflected back onto the phototransistor the output will begin to go lower. 2 front sensors will be connected to the "QREMiniBoard", rear sensor will be connected using

Pololu Distance Sensor with Pulse Width Output/Digital Output Small lidar based sensor can report presnece/distance of objects up to (TOTALMAX200cm-Digital, 300cm - PWM) Distance is chosen by configurating the jumpers with 0R resistors TF-LUNA MANUAL

Digital distance sensor - Sharp GP2Y0D810Z0F Sensor detects objects between 2 cm and 10cm

IR LED Reciver module Operating voltage: 2.7Vto 5.5V

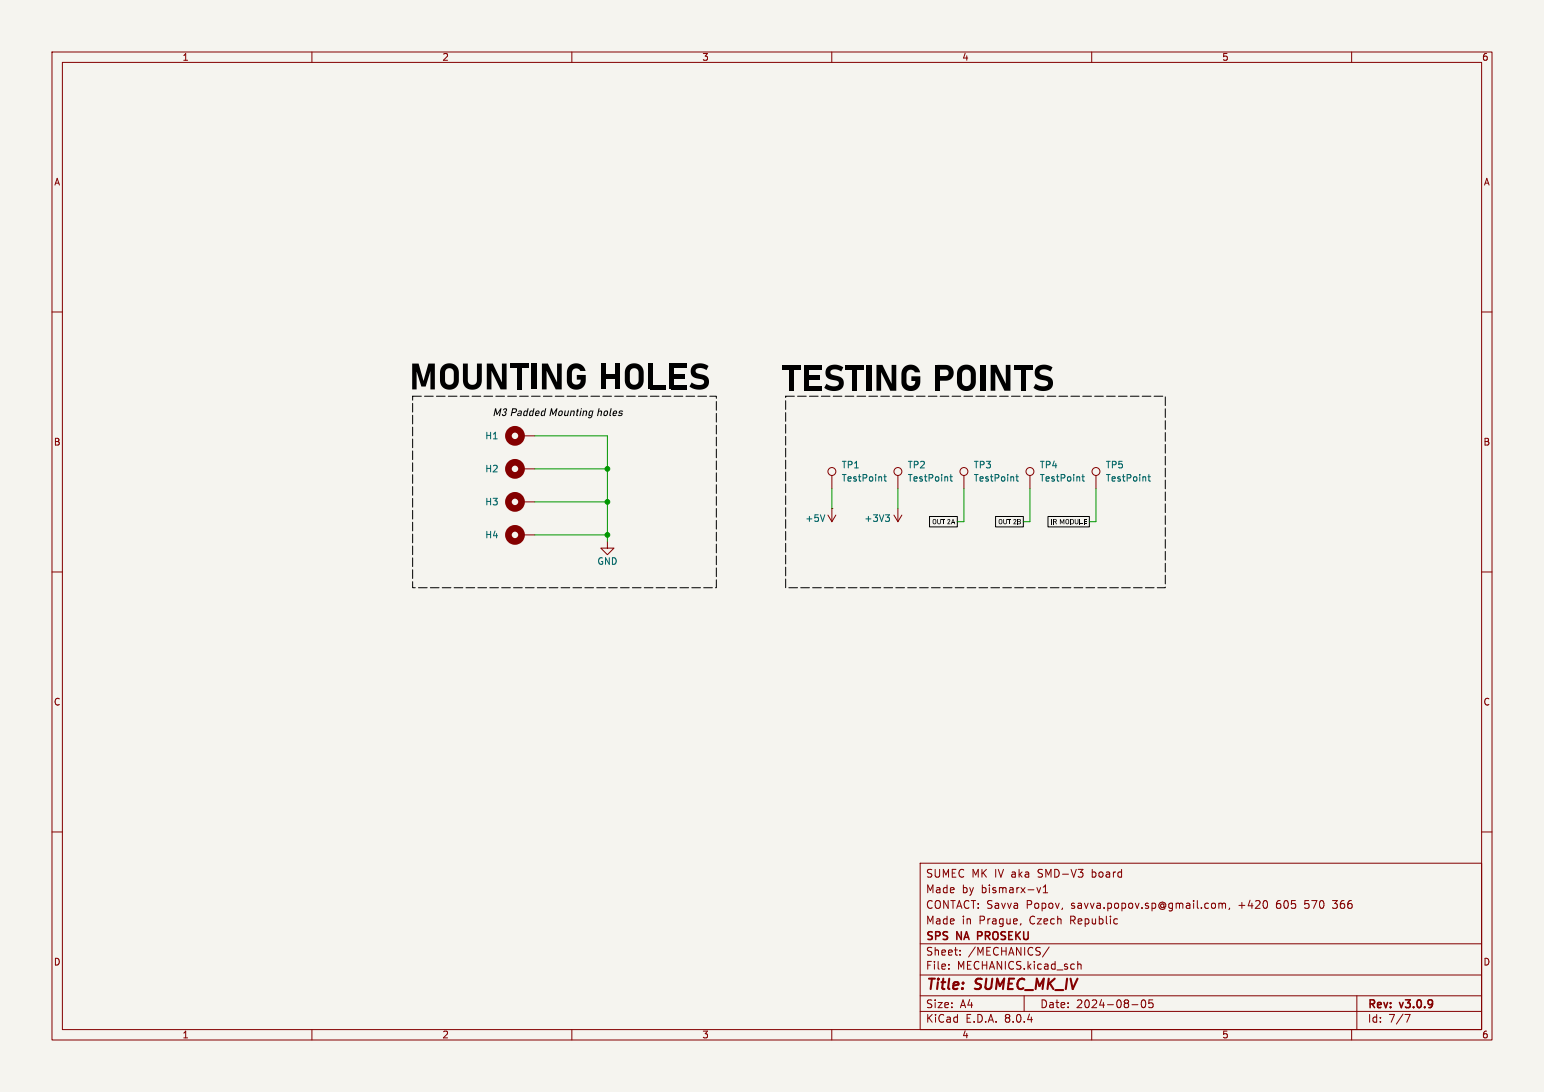
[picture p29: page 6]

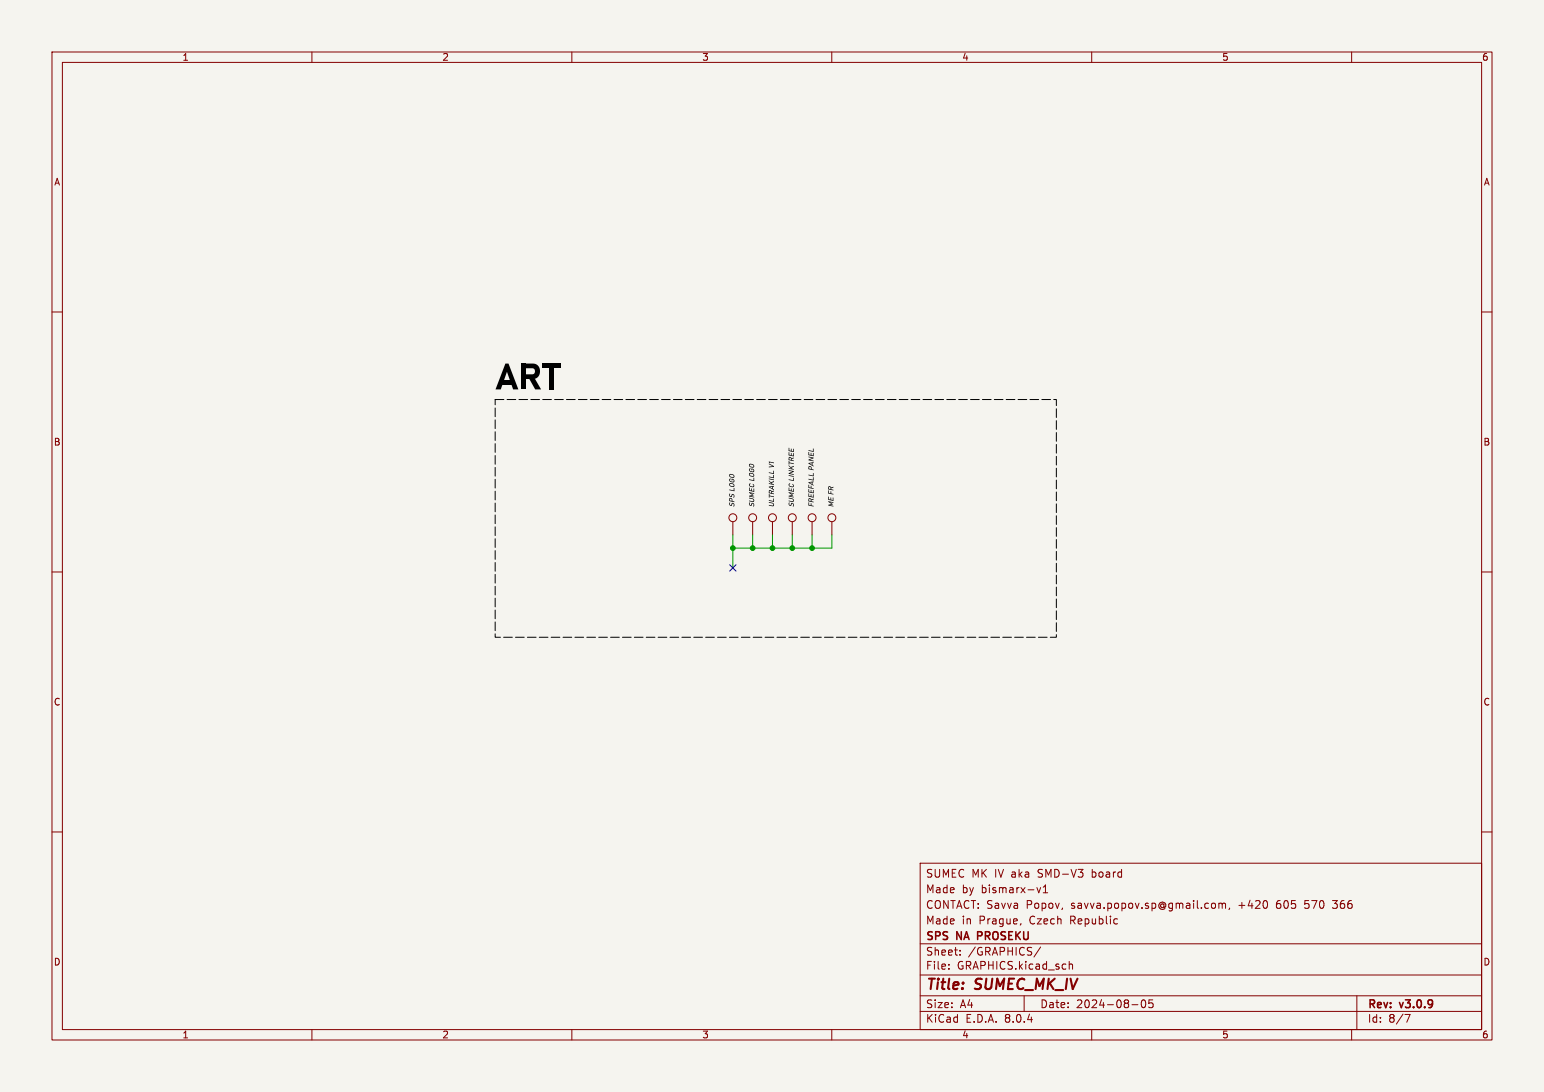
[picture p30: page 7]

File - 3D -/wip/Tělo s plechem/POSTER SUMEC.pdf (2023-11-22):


l MECHANICS: sIMON sTASTNY

o 3d modeling: jonas jary

01 PROGRAMMING: matej simacek, antonin havlik

m ELECTRICAL: SAVVA POPOV
h GOLD PRINTER GUY: lukas houdek

SUMEC - THE ROOMBA KILLER
MKII

~Who doesnt risk: doesnt drink champagne ~

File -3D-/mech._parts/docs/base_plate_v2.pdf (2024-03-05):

PROMÍTÁNÍ; [ISO E]; ČÍSLO VÝKRESU

MATERIÁL VÝCHOZÍ:
MATERÁL KONEČNÝ: POLOTOVAR:

TŘÍDA ODPADU: | INDEX: | ZMĚNA: | DATUM: | PODPIS:

PŘESNOST HMOTNOST N/A ISO 2768 | MĚŘÍTKO:
TOLEROVÁNÍ DLE ISO 8015

KRESLIL | jaryj | TŘÍDA | | STARÝ V.
DATUM | 30.01.2024 | SCHVÁLIL | | SESTAVA KUSOVNÍK

NÁZEV TYP: PLECH V2

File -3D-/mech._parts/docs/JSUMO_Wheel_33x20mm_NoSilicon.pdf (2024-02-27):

PROMÍTÁNÍ; [ISO E]; ČÍSLO VÝKRESU

MATERIÁL VÝCHOZÍ:
MATERÁL KONEČNÝ: POLOTOVAR:

TŘÍDA ODPADU: | INDEX: | ZMĚNA: | DATUM: | PODPIS:

PŘESNOST HMOTNOST N/A ISO 2768 | MĚŘÍTKO:
TOLEROVÁNÍ DLE ISO 8015

KRESLIL | 42060 | TŘÍDA | | STARÝ V.
DATUM | 29.01.2024 | SCHVÁLIL | | SESTAVA KUSOVNÍK

NÁZEV TYP:



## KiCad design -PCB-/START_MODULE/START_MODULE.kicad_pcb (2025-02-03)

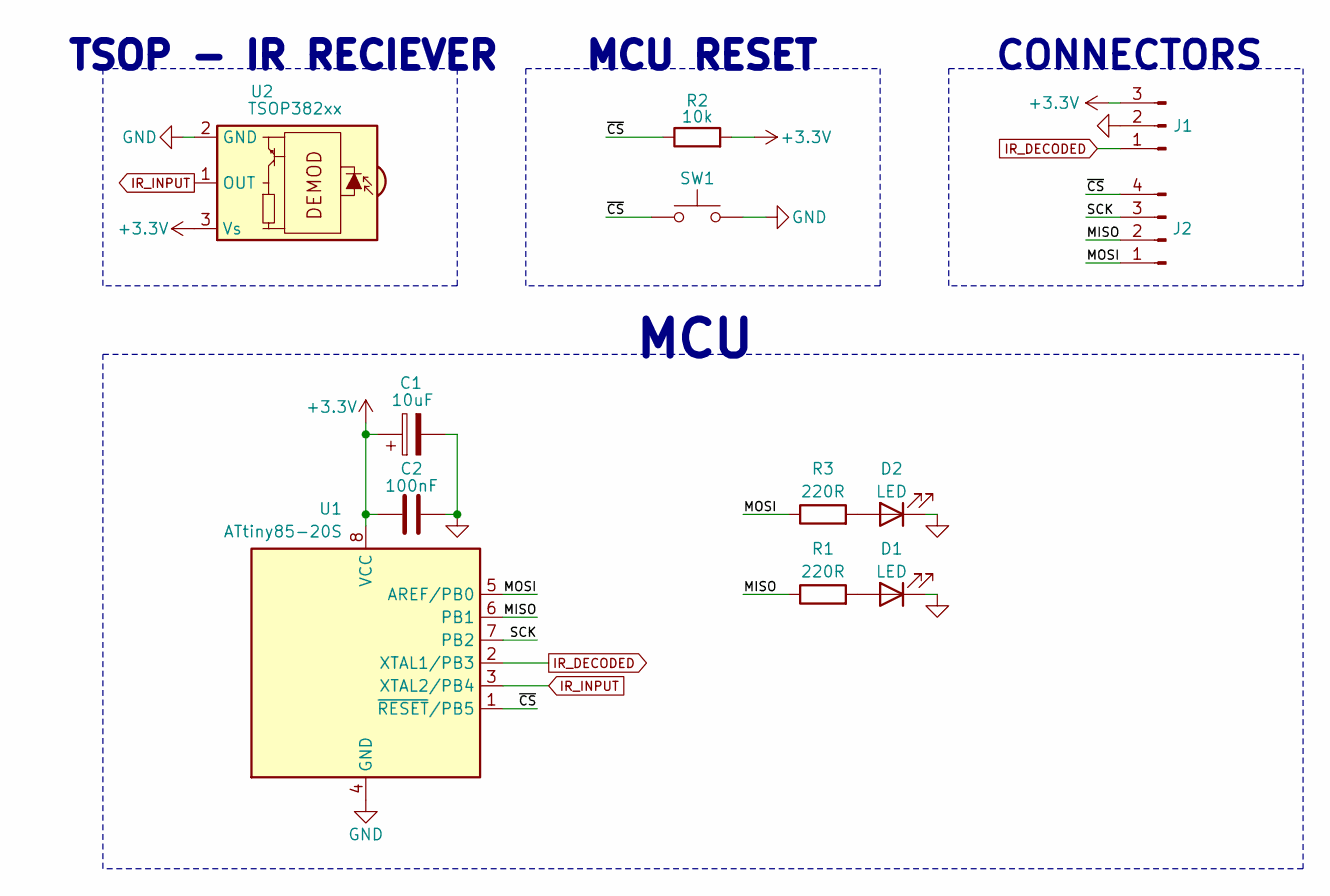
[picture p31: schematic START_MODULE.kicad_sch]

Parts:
C1: 10uF; CP_EIA-3216-18_Kemet-A_Pad1.58x1.35mm_HandSolder
C2: 100nF; C_0805_2012Metric_Pad1.18x1.45mm_HandSolder
D1, D2: LED; LED_0805_2012Metric_Pad1.15x1.40mm_HandSolder
J1: Conn_01x03_Pin; PinHeader_1x03_P2.54mm_Vertical
J2: Conn_01x04_Pin; PinHeader_1x04_P2.54mm_Vertical
R1, R3: 220R; R_0805_2012Metric_Pad1.20x1.40mm_HandSolder
R2: 10k; R_0805_2012Metric_Pad1.20x1.40mm_HandSolder
SW1: SW_Push; SW_SPST_EVQPE1
U1: ATtiny85-20S; SOIC-8W_5.3x5.3mm_P1.27mm
U2: TSOP382xx; Vishay_MINICAST-3Pin

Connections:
+3.3V: C1.1, C2.1, J1.3, R2.2, U1.8 (VCC), U2.3 (Vs)
/MISO: J2.2, R1.1, U1.6 (PB1)
/MOSI: J2.1, R3.1, U1.5 (AREF/PB0)
/SCK: J2.3, U1.7 (PB2)
/~CS: J2.4, R2.1, SW1.2, U1.1 (~RESET/PB5)
GND: C1.2, C2.2, D1.1 (K), D2.1 (K), J1.2, SW1.1, U1.4 (GND), U2.2 (GND)
IR_DECODED: J1.1, U1.2 (XTAL1/PB3)
IR_INPUT: U1.3 (XTAL2/PB4), U2.1 (OUT)
unnamed: D1.2 (A), R1.2
unnamed: D2.2 (A), R3.2

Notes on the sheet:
MCU
TSOP - IR RECIEVER
CONNECTORS
MCU RESET

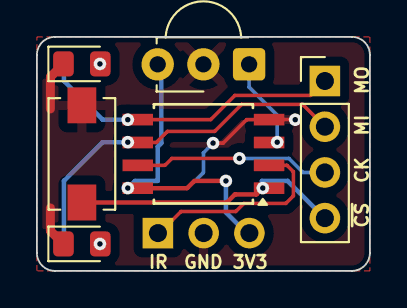
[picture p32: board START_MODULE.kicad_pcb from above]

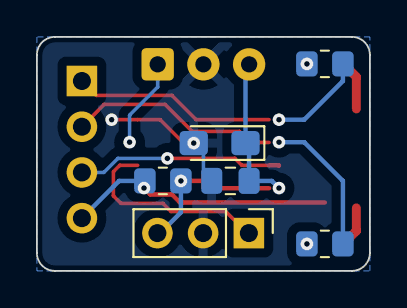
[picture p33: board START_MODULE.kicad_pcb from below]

Board: 2 copper layers, 18.5 x 13.0 mm, 12 parts (6 on the bottom side), 10 nets.

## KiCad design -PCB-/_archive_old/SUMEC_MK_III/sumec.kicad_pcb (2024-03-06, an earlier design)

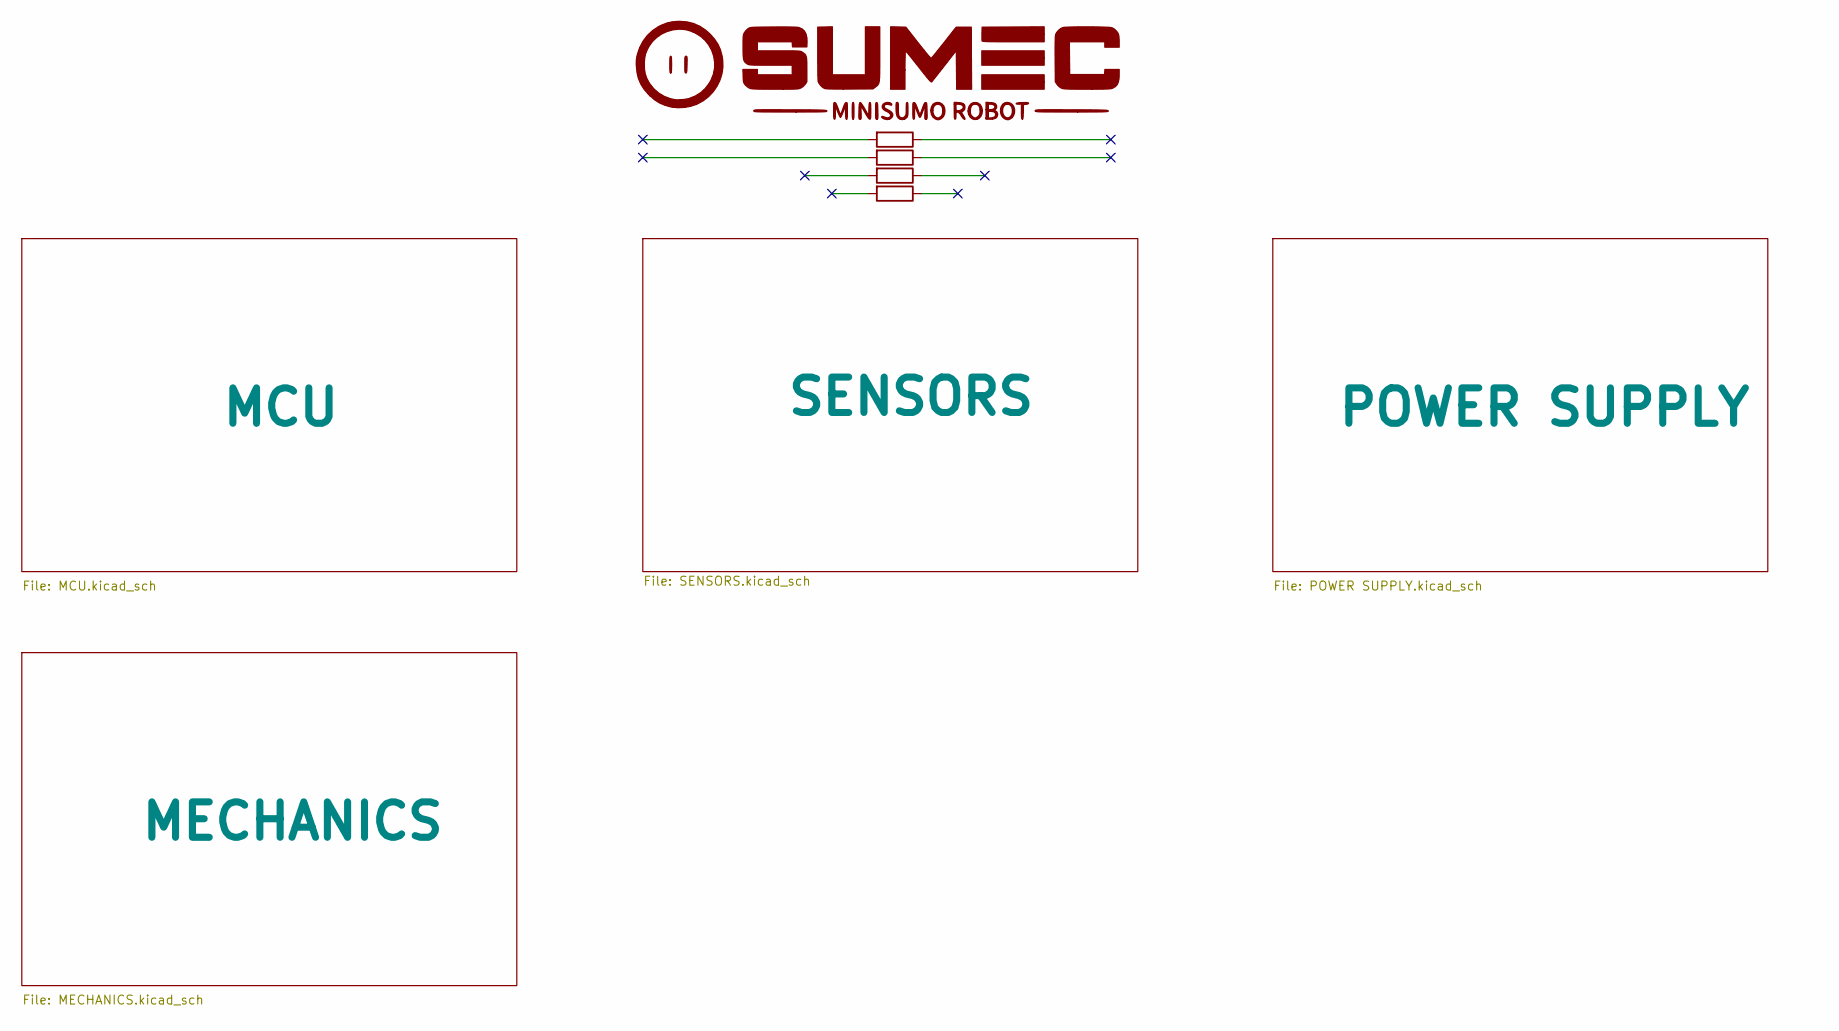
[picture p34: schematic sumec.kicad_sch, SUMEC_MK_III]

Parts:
R4: R; SPS LOGO
R12: R; VIGIL 2
R20: R; R2D2
R21: R; Logo

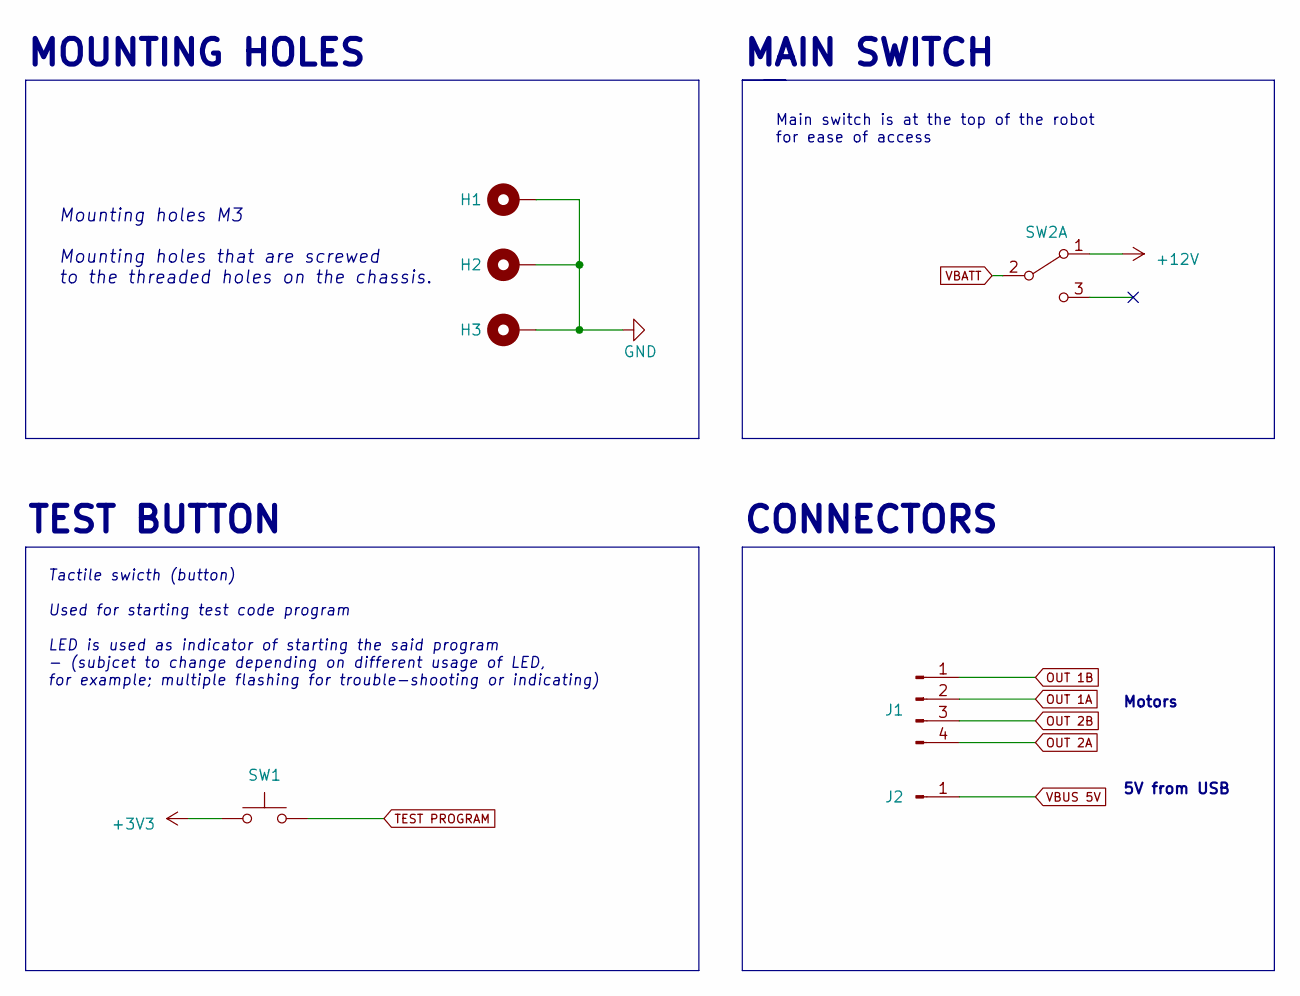
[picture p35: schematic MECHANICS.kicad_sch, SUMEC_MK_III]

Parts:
H1, H2, H3: MountingHole_Pad; MountingHole_3.2mm_M3_Pad
J1: Conn_01x04_Pin; JST_XH_B4B-XH-A_1x04_P2.50mm_Vertical
J2: Conn_01x01_Pin; SolderWire-0.1sqmm_1x01_D0.4mm_OD1mm
SW1: SW_Push; SW_SPST_B3U-1000P
SW2: SW_DPDT_x2; Custom_SPDT_4.8mm_Switch

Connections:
+3V3: SW1.1; also elsewhere on the board
+12V: SW2.1 (A); also elsewhere on the board
GND: H1.1, H2.1, H3.1; also elsewhere on the board
OUT 1A: J1.2; also elsewhere on the board
OUT 1B: J1.1; also elsewhere on the board
OUT 2A: J1.4; also elsewhere on the board
OUT 2B: J1.3; also elsewhere on the board
TEST PROGRAM: SW1.2; also elsewhere on the board
VBATT: SW2.2 (B); also elsewhere on the board
VBUS 5V: J2.1; also elsewhere on the board

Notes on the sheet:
MOUNTING HOLES
Mounting holes M3 Mounting holes that are screwed to the threaded holes on the chassis.
MAIN SWITCH
Motors
TEST BUTTON
Main switch is at the top of the robot for ease of access
5V from USB
CONNECTORS
Tactile swicth (button) Used for starting test code program LED is used as indicator of starting the said program - (subjcet to change depending on different usage of LED, for example; multiple flashing for trouble-shooting or indicating)

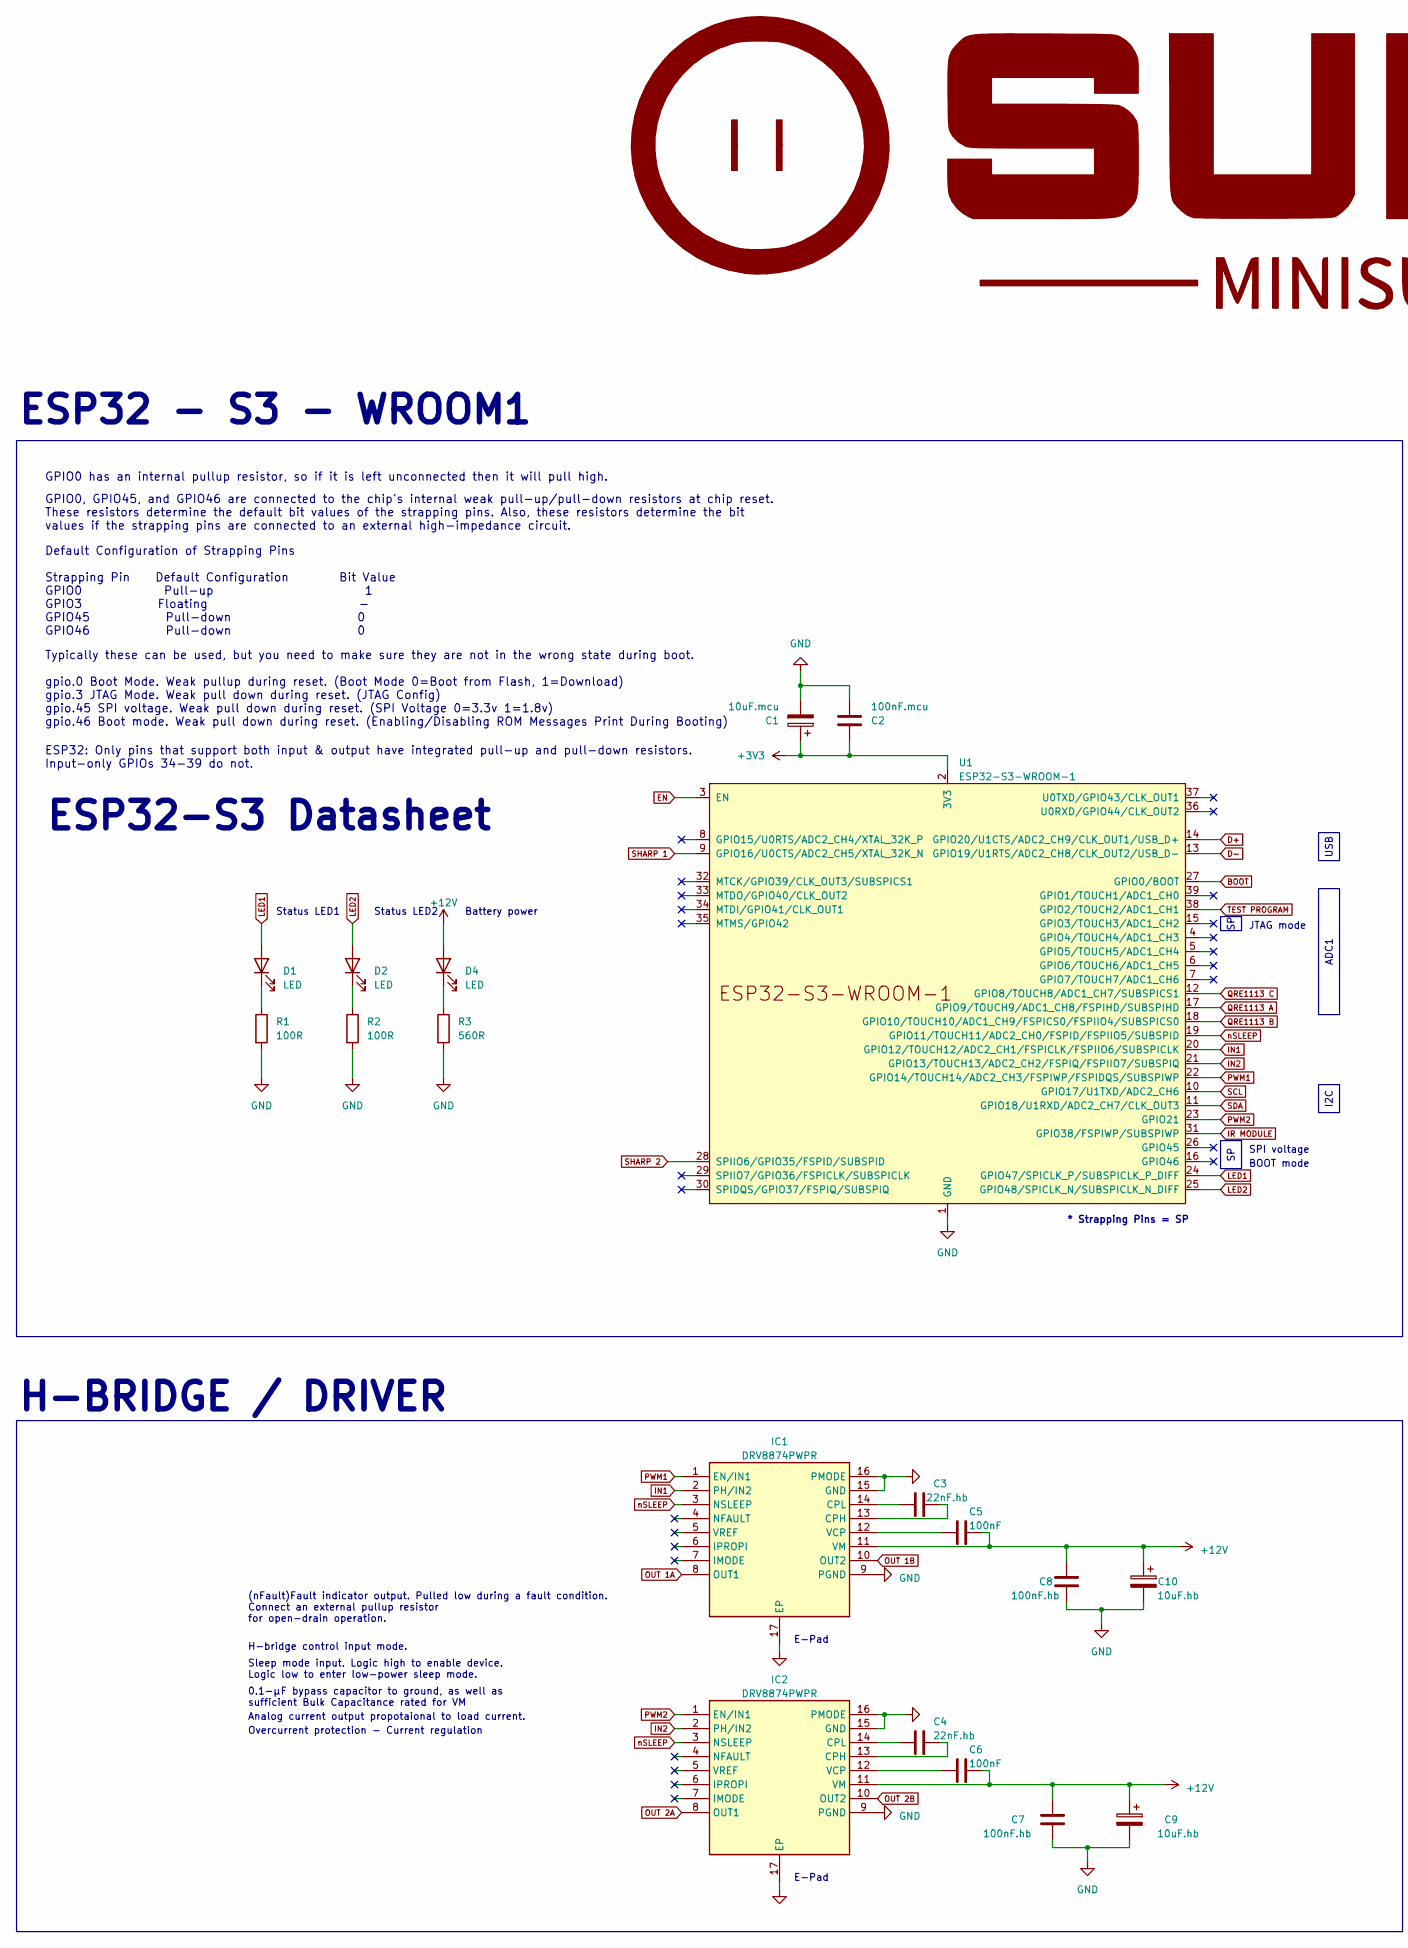
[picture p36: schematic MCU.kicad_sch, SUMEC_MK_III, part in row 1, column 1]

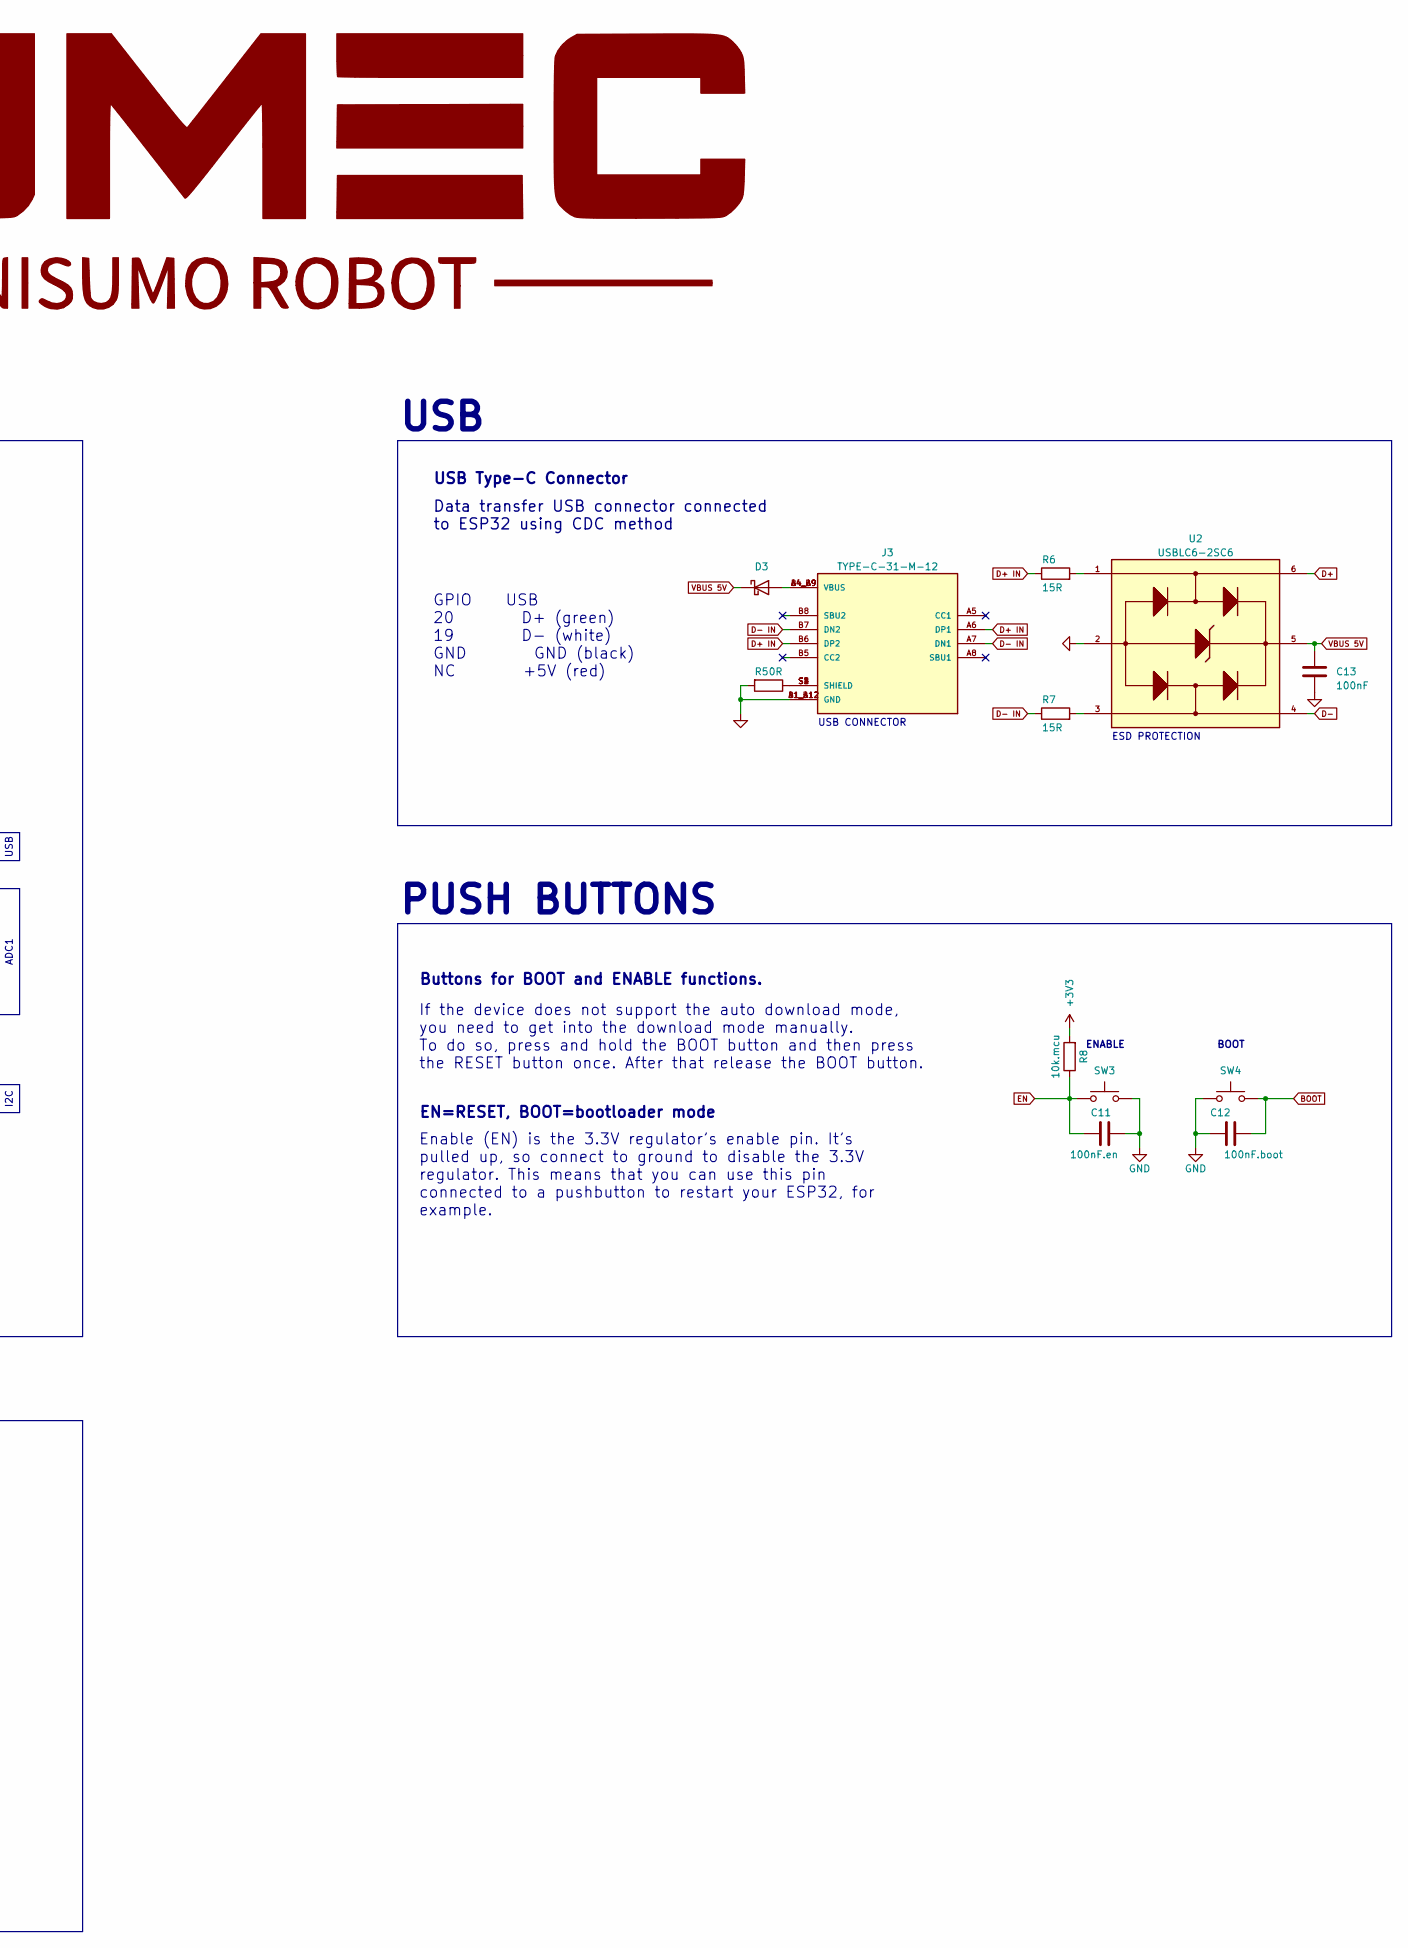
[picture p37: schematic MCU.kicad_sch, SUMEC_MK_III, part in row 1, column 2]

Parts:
C1: 10uF.mcu; CP_EIA-3216-18_Kemet-A_Pad1.58x1.35mm_HandSolder
C2: 100nF.mcu; C_0805_2012Metric_Pad1.18x1.45mm_HandSolder
C3, C4: 22nF.hb; C_0805_2012Metric_Pad1.18x1.45mm_HandSolder
C5, C6, C13: 100nF; C_0805_2012Metric_Pad1.18x1.45mm_HandSolder
C7, C8: 100nF.hb; C_0805_2012Metric_Pad1.18x1.45mm_HandSolder
C9, C10: 10uF.hb; CP_EIA-3216-18_Kemet-A_Pad1.58x1.35mm_HandSolder
C11: 100nF.en; C_0805_2012Metric_Pad1.18x1.45mm_HandSolder
C12: 100nF.boot; C_0805_2012Metric_Pad1.18x1.45mm_HandSolder
D1, D2, D4: LED; LED_0805_2012Metric_Pad1.15x1.40mm_HandSolder
D3: D_Schottky; D_1206_3216Metric_Pad1.42x1.75mm_HandSolder
IC1, IC2: DRV8874PWPR; DRV8874; Manufacturer_Part_Number DRV8874PWPR; Mouser Part Number 595-DRV8874PWPR
J3: TYPE-C-31-M-12; USB_Type_C; PARTREV 2020.12.08
R1, R2: 100R; R_0805_2012Metric_Pad1.20x1.40mm_HandSolder
R3: 560R; R_0805_2012Metric_Pad1.20x1.40mm_HandSolder
R5: 0R; R_1206_3216Metric_Pad1.30x1.75mm_HandSolder
R6, R7: 15R; R_0805_2012Metric_Pad1.20x1.40mm_HandSolder
R8: 10k.mcu; R_0805_2012Metric_Pad1.20x1.40mm_HandSolder
SW3, SW4: SW_Push; SW_SPST_B3U-1000P
U1: ESP32-S3-WROOM-1
U2: USBLC6-2SC6; TSOT-23-6_HandSoldering

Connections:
+3V3: C1.1, C2.1, R8.2, U1.2 (3V3); also elsewhere on the board
+12V: C5.1, C6.1, C7.2, C8.2, C9.1, C10.1, D4.2 (A), IC1.11 (VM), IC2.11 (VM); also elsewhere on the board
BOOT: C12.1, SW4.2, U1.27 (GPIO0/BOOT)
D+: U1.14 (GPIO20/U1CTS/ADC2_CH9/CLK_OUT1/USB_D+), U2.6
D+ IN: J3.A6 (DP1), J3.B6 (DP2), R6.1
D-: U1.13 (GPIO19/U1RTS/ADC2_CH8/CLK_OUT2/USB_D-), U2.4
D- IN: J3.A7 (DN1), J3.B7 (DN2), R7.1
EN: C11.1, R8.1, SW3.2, U1.3 (EN)
GND: C1.2, C2.2, C7.1, C8.1, C9.2, C10.2, C11.2, C12.2, C13.2, IC1.9 (PGND), IC1.15 (GND), IC1.16 (PMODE), IC1.17 (EP), IC2.9 (PGND), IC2.15 (GND), IC2.16 (PMODE), IC2.17 (EP), J3.A1_B12 (GND), J3.B1_A12 (GND), R1.2, R2.2, R3.2, R5.2, SW3.1, SW4.1, U1.1 (GND), U1.40 (GND), U1.41 (GND), U2.2; also elsewhere on the board
IN1: IC1.2 (PH/IN2), U1.20 (GPIO12/TOUCH12/ADC2_CH1/FSPICLK/FSPIIO6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)
IN2: IC2.2 (PH/IN2), U1.21 (GPIO13/TOUCH13/ADC2_CH2/FSPIQ/FSPIIO7/S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)
IR MODULE: U1.31 (GPIO38/FSPIWP/SUBSPIWP); also elsewhere on the board
LED1: D1.2 (A), U1.24 (GPIO47/SPICLK_P/SUBSPICLK_P_DIFF)
LED2: D2.2 (A), U1.25 (GPIO48/SPICLK_N/SUBSPICLK_N_DIFF)
unnamed: D1.1 (K), R1.1
unnamed: D2.1 (K), R2.1
unnamed: D3.2 (A), J3.A4_B9 (VBUS), J3.B4_A9 (VBUS)
unnamed: D4.1 (K), R3.1
unnamed: C3.2, IC1.13 (CPH)
unnamed: C3.1, IC1.14 (CPL)
unnamed: C5.2, IC1.12 (VCP)
unnamed: C4.2, IC2.13 (CPH)
unnamed: C4.1, IC2.14 (CPL)
unnamed: C6.2, IC2.12 (VCP)
unnamed: J3.S1 (SHIELD), J3.S2 (SHIELD), J3.S3 (SHIELD), J3.S4 (SHIELD), R5.1
unnamed: R6.2, U2.1
unnamed: R7.2, U2.3
OUT 1A: IC1.8 (OUT1); also elsewhere on the board
OUT 1B: IC1.10 (OUT2); also elsewhere on the board
OUT 2A: IC2.8 (OUT1); also elsewhere on the board
OUT 2B: IC2.10 (OUT2); also elsewhere on the board
PWM1: IC1.1 (EN/IN1), U1.22 (GPIO14/TOUCH14/ADC2_CH3/FSPIWP/FSPIDQS/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)
PWM2: IC2.1 (EN/IN1), U1.23 (GPIO21)
QRE1113 A: U1.17 (GPIO9/TOUCH9/ADC1_CH8/FSPIHD/SUBSPIHD); also elsewhere on the board
QRE1113 B: U1.18 (GPIO10/TOUCH10/ADC1_CH9/FSPICS0/FSPIIO4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); also elsewhere on the board
QRE1113 C: U1.12 (GPIO8/TOUCH8/ADC1_CH7/SUBSPICS1); also elsewhere on the board
SCL: U1.10 (GPIO17/U1TXD/ADC2_CH6); also elsewhere on the board
SDA: U1.11 (GPIO18/U1RXD/ADC2_CH7/CLK_OUT3); also elsewhere on the board
SHARP 1: U1.9 (GPIO16/U0CTS/ADC2_CH5/XTAL_32K_N); also elsewhere on the board
SHARP 2: U1.28 (SPIIO6/GPIO35/FSPID/SUBSPID); also elsewhere on the board
TEST PROGRAM: U1.38 (GPIO2/TOUCH2/ADC1_CH1); also elsewhere on the board
VBUS 5V: C13.1, D3.1 (K), U2.5; also elsewhere on the board
nSLEEP: IC1.3 (NSLEEP), IC2.3 (NSLEEP), U1.19 (GPIO11/TOUCH11/ADC2_CH0/FSPID/FSPIIO5/S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)

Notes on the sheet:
ADC1
USB
I2C
0.1-µF bypass capacitor to ground, as well as sufficient Bulk Capacitance rated for VM
SPI voltage
Enable (EN) is the 3.3V regulator’s enable pin. It’s pulled up, so connect to ground to disable the 3.3V regulator. This means that you can use this pin connected to a pushbutton to restart your ESP32, for example.
USB CONNECTOR
Status LED2
Sleep mode input. Logic high to enable device. Logic low to enter low-power sleep mode.
USB Type-C Connector
GPIO0, GPIO45, and GPIO46 are connected to the chip's internal weak pull-up/pull-down resistors at chip reset. These resistors determine the default bit values of the strapping pins. Also, these resistors determine the bit values if the strapping pins are connected to an external high-impedance cir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
E-Pad
Overcurrent protection - Current regulation
ENABLE
Analog current output propotaional to load current.
GPIO USB 20 D+ (green) 19 D- (white) GND GND (black) NC +5V (red)
H-BRIDGE / DRIVER
Status LED1
H-bridge control input mode.
BOOT mode
If the device does not support the auto download mode, you need to get into the download mode manually. To do so, press and hold the BOOT button and then press the RESET button once. After that release the BOOT button.
* Strapping Pins = SP
Battery power
ESP32 - S3 - WROOM1
Default Configuration of Strapping Pins Strapping Pin Default Configuration Bit Value GPIO0 Pull-up 1 GPIO3 Floating - GPIO45 Pull-down 0 GPIO46 Pull-down 0
JTAG mode
PUSH BUTTONS
GPIO0 has an internal pullup resistor, so if it is left unconnected then it will pull high.
ESD PROTECTION
Buttons for BOOT and ENABLE functions.
Typically these can be used, but you need to make sure they are not in the wrong state during boot. gpio.0 Boot Mode. Weak pullup during reset. (Boot Mode 0=Boot from Flash, 1=Download) gpio.3 JTAG Mode. Weak pull down during reset. (JTAG Config) gpio.45 SPI voltage. Weak pull down during reset. (S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
ESP32: Only pins that support both input & output have integrated pull-up and pull-down resistors. Input-only GPIOs 34-39 do not.
ESP32-S3 Datasheet
EN=RESET, BOOT=bootloader mode
Data transfer USB connector connected to ESP32 using CDC method
BOOT
(nFault)Fault indicator output. Pulled low during a fault condition. Connect an external pullup resistor for open-drain operation.

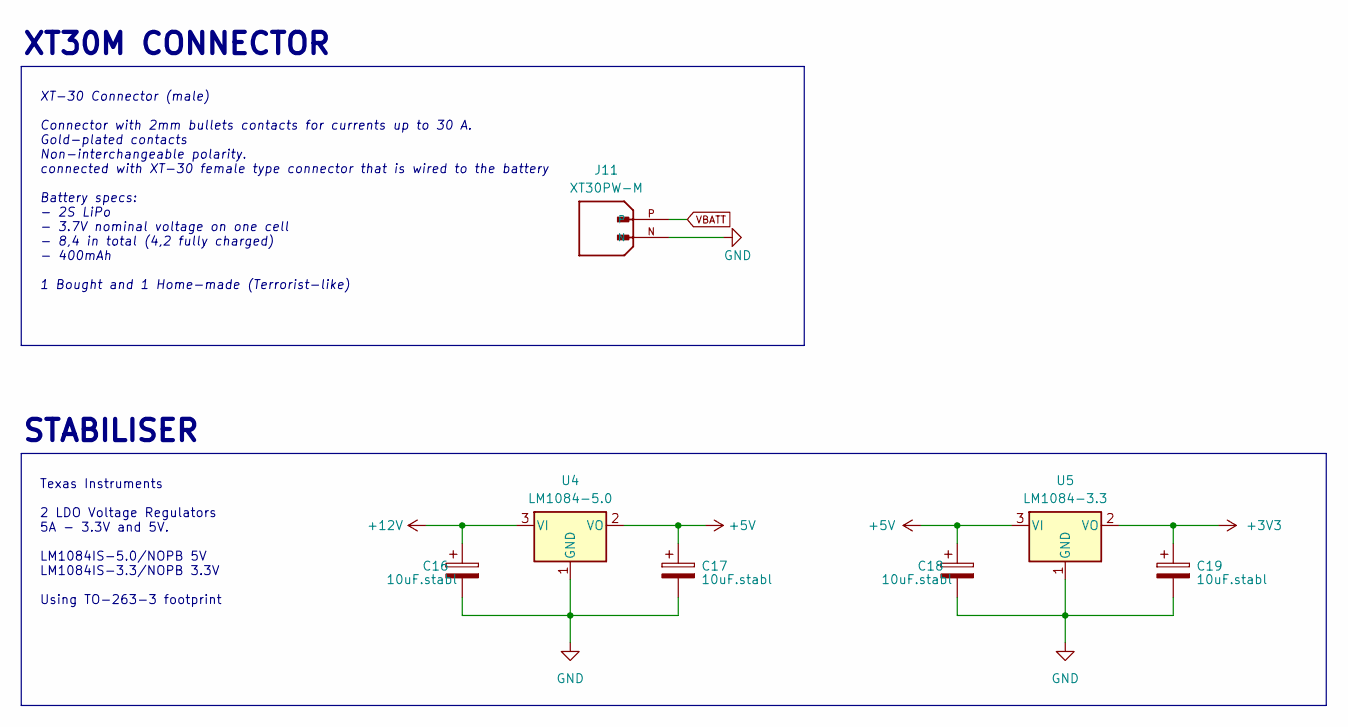
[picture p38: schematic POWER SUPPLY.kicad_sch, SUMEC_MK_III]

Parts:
C16, C17, C18, C19: 10uF.stabl; CP_EIA-3216-18_Kemet-A_Pad1.58x1.35mm_HandSolder
J11: XT30PW-M; AMASS_XT30PW-M; PARTREV 1.2
U4: LM1084-5.0; TO-263-3_TabPin2
U5: LM1084-3.3; TO-263-3_TabPin2

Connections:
+3V3: C19.1, U5.2 (VO); also elsewhere on the board
+5V: C17.1, C18.1, U4.2 (VO), U5.3 (VI); also elsewhere on the board
+12V: C16.1, U4.3 (VI); also elsewhere on the board
GND: C16.2, C17.2, C18.2, C19.2, J11.N, U4.1 (GND), U5.1 (GND); also elsewhere on the board
VBATT: J11.P; also elsewhere on the board

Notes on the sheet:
Texas Instruments 2 LDO Voltage Regulators 5A - 3.3V and 5V. LM1084IS-5.0/NOPB 5V LM1084IS-3.3/NOPB 3.3V Using TO-263-3 footprint
XT-30 Connector (male) Connector with 2mm bullets contacts for currents up to 30 A. Gold-plated contacts Non-interchangeable polarity. connected with XT-30 female type connector that is wired to the battery Battery specs: - 2S LiPo - 3.7V nominal voltage on one cell - 8,4 in total (4,2 fully charge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
STABILISER
XT30M CONNECTOR

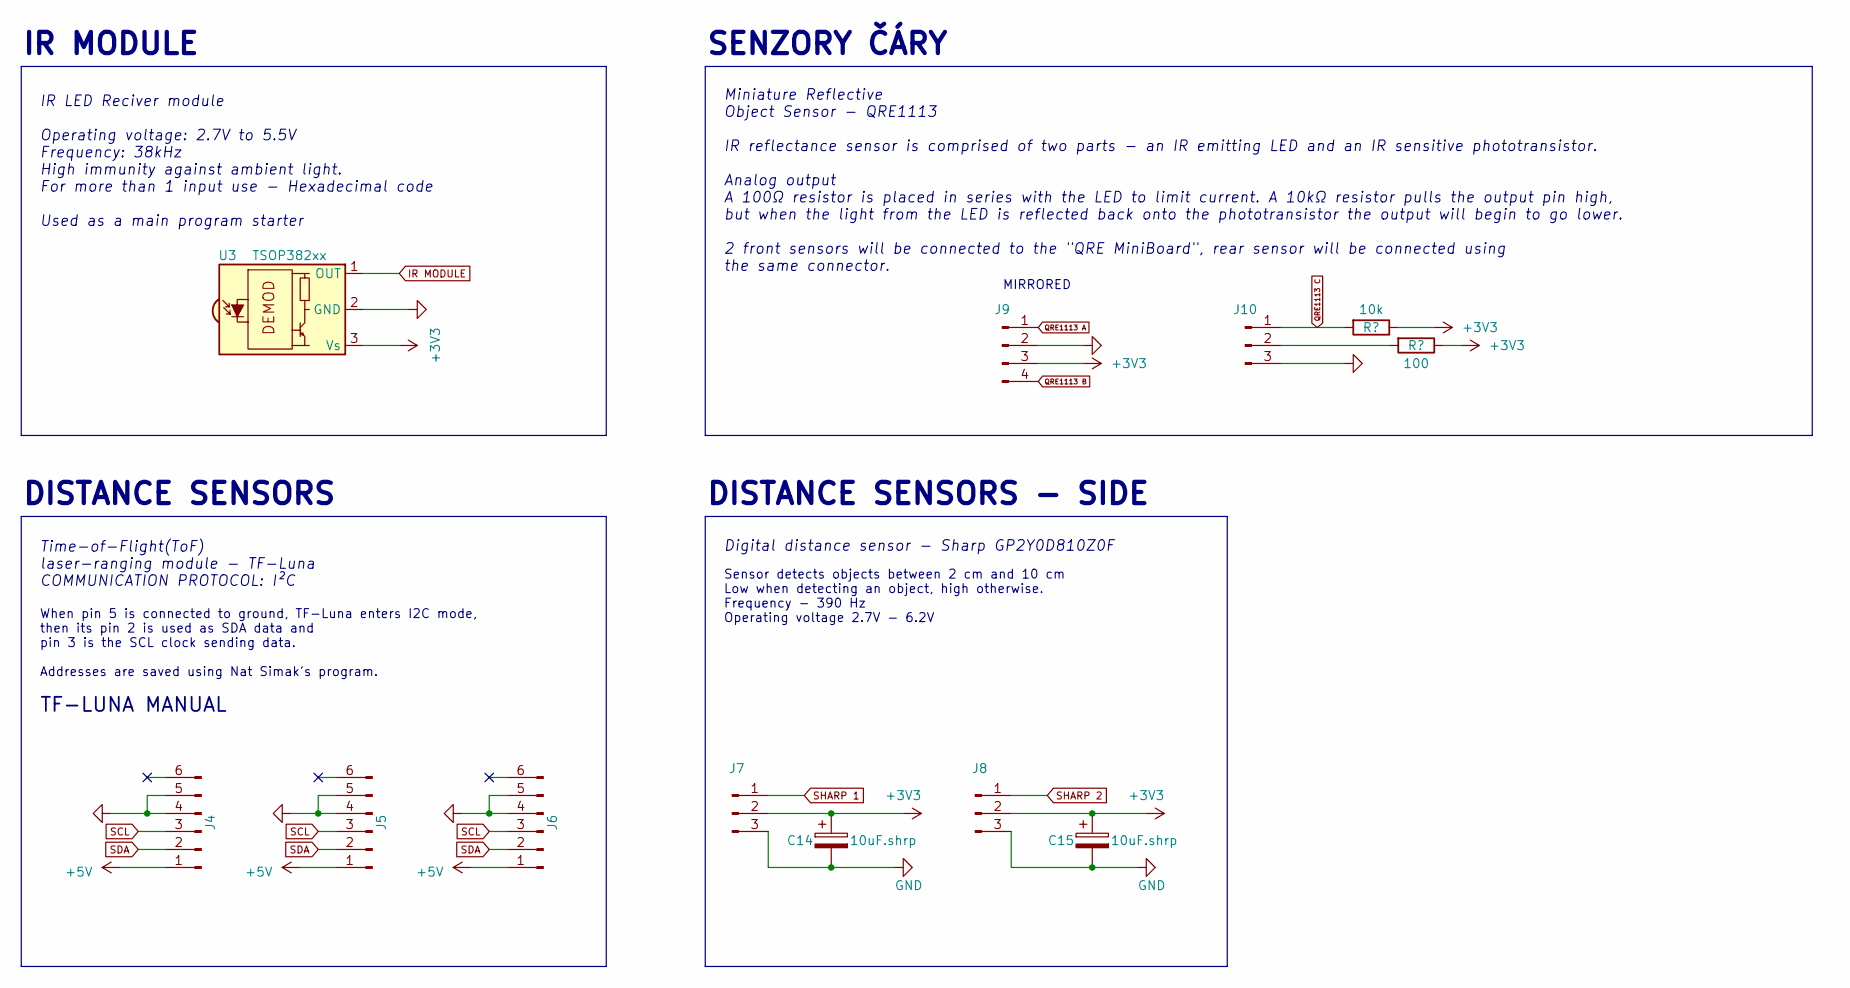
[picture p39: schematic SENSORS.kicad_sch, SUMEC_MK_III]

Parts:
C14, C15: 10uF.shrp; CP_EIA-3216-18_Kemet-A_Pad1.58x1.35mm_HandSolder
J4, J5, J6: Conn_01x06_Pin; Molex_PicoBlade_53398-0671_1x06-1MP_P1.25mm_Vertical
J7, J8, J10: Conn_01x03_Pin; Molex_PicoBlade_53398-0371_1x03-1MP_P1.25mm_Vertical
J9: Conn_01x04_Pin; Molex_PicoBlade_53398-0471_1x04-1MP_P1.25mm_Vertical
R9: 10k; R_0805_2012Metric_Pad1.20x1.40mm_HandSolder
R10: 100; R_0805_2012Metric_Pad1.20x1.40mm_HandSolder
U3: TSOP382xx; TSOP

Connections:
+3V3: C14.1, C15.1, J7.2, J8.2, J9.3, R9.1, R10.1, U3.3 (Vs); also elsewhere on the board
+5V: J4.1, J5.1, J6.1; also elsewhere on the board
GND: C14.2, C15.2, J4.4, J4.5, J5.4, J5.5, J6.4, J6.5, J7.3, J8.3, J9.2, J10.3, U3.2 (GND); also elsewhere on the board
IR MODULE: U3.1 (OUT); also elsewhere on the board
unnamed: J10.2, R10.2
QRE1113 A: J9.1; also elsewhere on the board
QRE1113 B: J9.4; also elsewhere on the board
QRE1113 C: J10.1, R9.2; also elsewhere on the board
SCL: J4.3, J5.3, J6.3; also elsewhere on the board
SDA: J4.2, J5.2, J6.2; also elsewhere on the board
SHARP 1: J7.1; also elsewhere on the board
SHARP 2: J8.1; also elsewhere on the board

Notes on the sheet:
Time-of-Flight(ToF) laser-ranging module - TF-Luna COMMUNICATION PROTOCOL: I²C
IR LED Reciver module Operating voltage: 2.7V to 5.5V Frequency: 38kHz High immunity against ambient light. For more than 1 input use - Hexadecimal code Used as a main program starter
Digital distance sensor - Sharp GP2Y0D810Z0F
IR MODULE
SENZORY ČÁRY
When pin 5 is connected to ground, TF-Luna enters I2C mode, then its pin 2 is used as SDA data and pin 3 is the SCL clock sending data. Addresses are saved using Nat Simak's program.
Sensor detects objects between 2 cm and 10 cm Low when detecting an object, high otherwise. Frequency - 390 Hz Operating voltage 2.7V - 6.2V
Miniature Reflective Object Sensor - QRE1113 IR reflectance sensor is comprised of two parts - an IR emitting LED and an IR sensitive phototransistor. Analog output A 100Ω resistor is placed in series with the LED to limit current. A 10kΩ resistor pulls the output pin high, but when the light from 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
TF-LUNA MANUAL
DISTANCE SENSORS
MIRRORED
DISTANCE SENSORS - SIDE

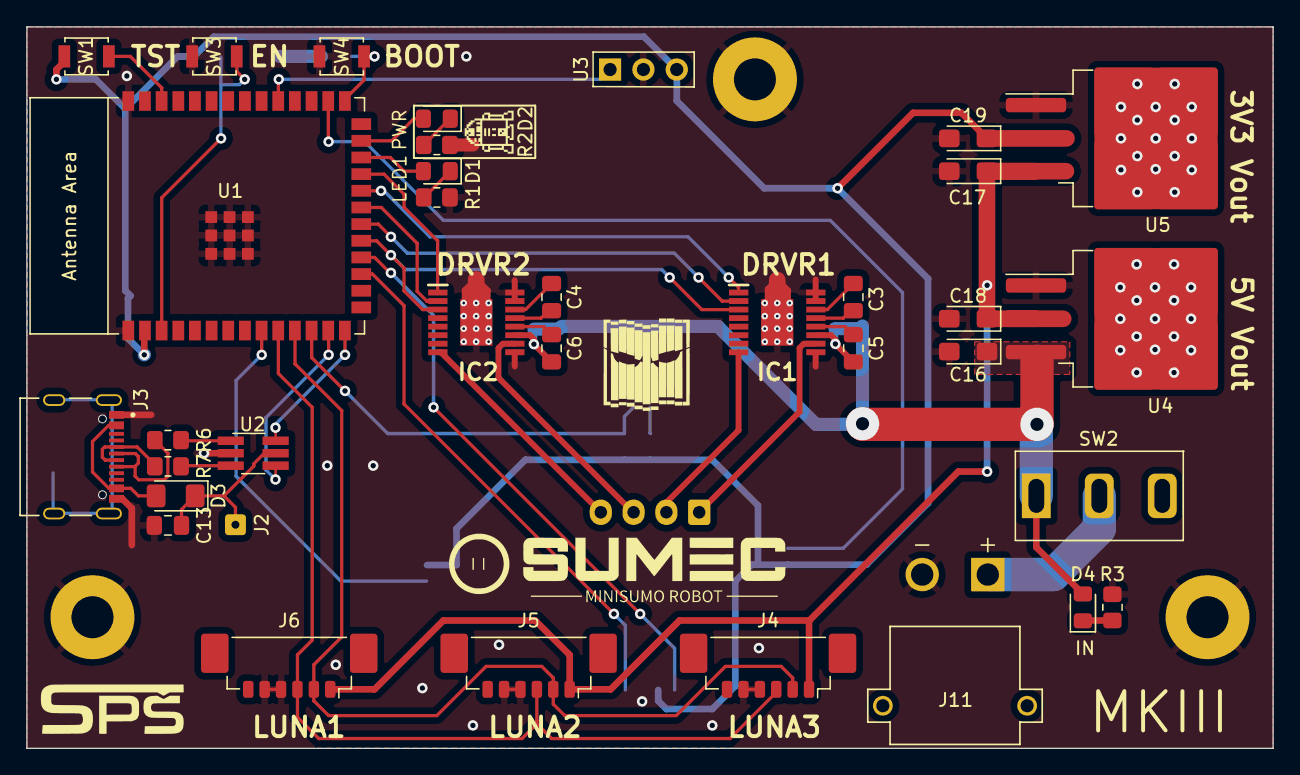
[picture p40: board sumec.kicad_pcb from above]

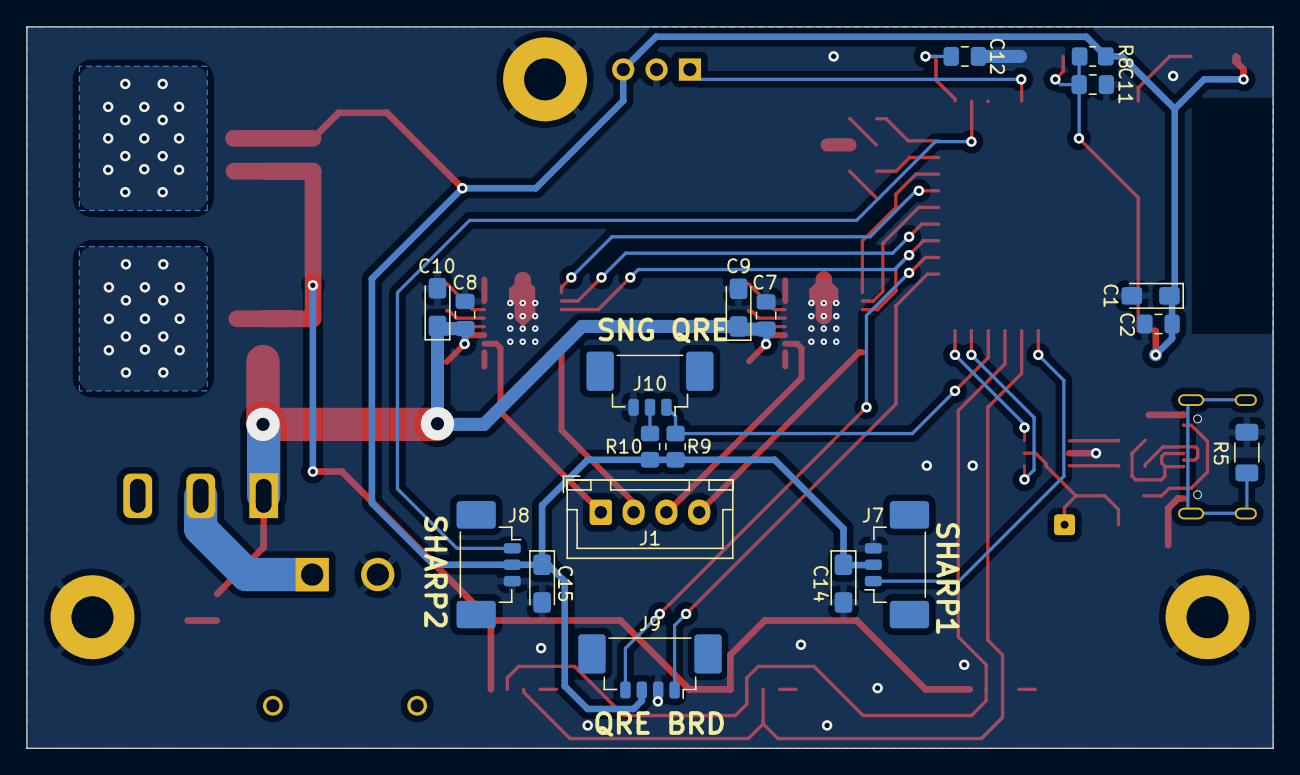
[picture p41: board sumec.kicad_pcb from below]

Board: 2 copper layers, 95.0 x 55.0 mm, 61 parts (19 on the bottom side), 46 nets.

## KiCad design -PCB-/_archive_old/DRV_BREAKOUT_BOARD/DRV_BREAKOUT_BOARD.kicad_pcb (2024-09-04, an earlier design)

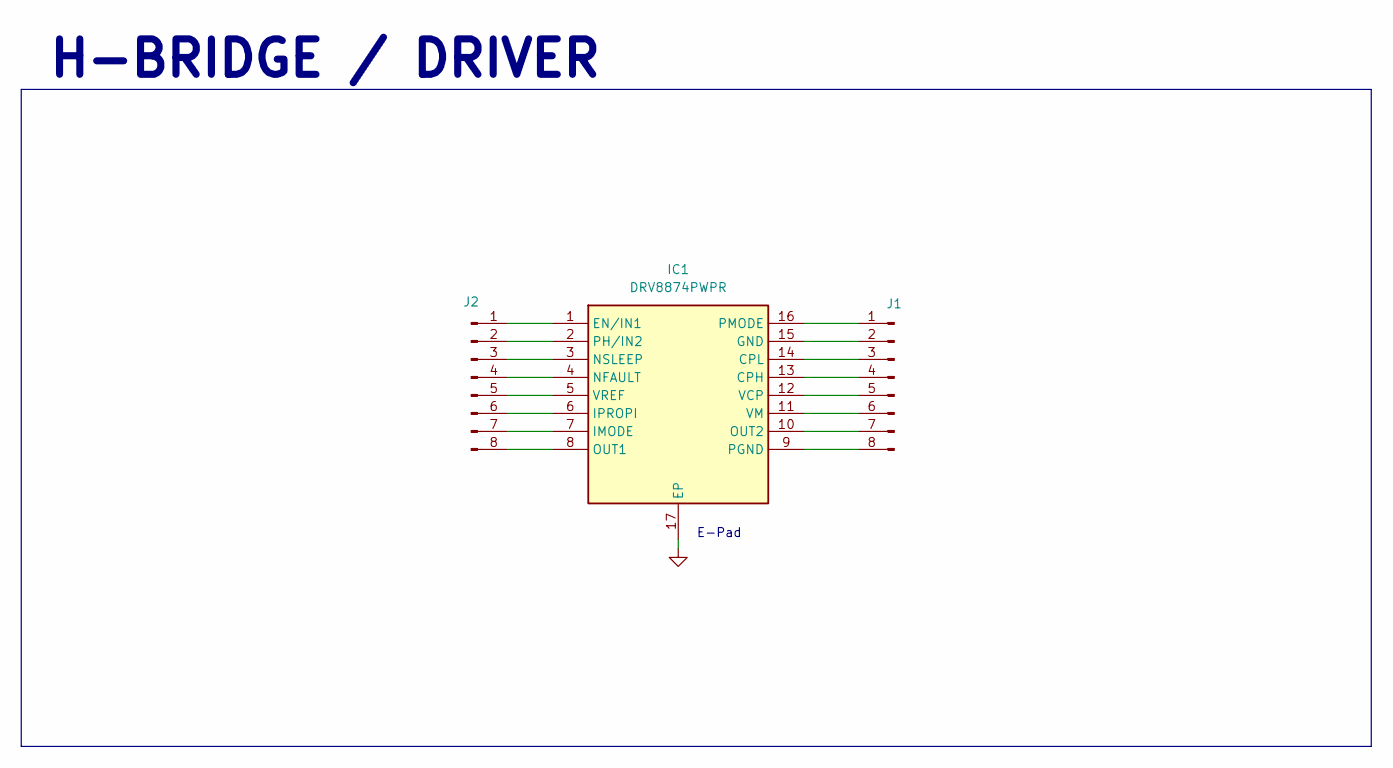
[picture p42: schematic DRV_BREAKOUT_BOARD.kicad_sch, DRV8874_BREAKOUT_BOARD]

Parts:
IC1: DRV8874PWPR; DRV8874; Manufacturer_Part_Number DRV8874PWPR; Mouser Part Number 595-DRV8874PWPR
J1, J2: Conn_01x08_Pin; PinHeader_1x08_P2.54mm_Vertical

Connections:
GND: IC1.17 (EP)
unnamed: IC1.13 (CPH), J1.4
unnamed: IC1.14 (CPL), J1.3
unnamed: IC1.1 (EN/IN1), J2.1
unnamed: IC1.15 (GND), J1.2
unnamed: IC1.7 (IMODE), J2.7
unnamed: IC1.6 (IPROPI), J2.6
unnamed: IC1.4 (NFAULT), J2.4
unnamed: IC1.3 (NSLEEP), J2.3
unnamed: IC1.8 (OUT1), J2.8
unnamed: IC1.10 (OUT2), J1.7
unnamed: IC1.9 (PGND), J1.8
unnamed: IC1.2 (PH/IN2), J2.2
unnamed: IC1.16 (PMODE), J1.1
unnamed: IC1.12 (VCP), J1.5
unnamed: IC1.11 (VM), J1.6
unnamed: IC1.5 (VREF), J2.5

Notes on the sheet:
H-BRIDGE / DRIVER
E-Pad


Board: 2 copper layers, 18.8 x 21.3 mm, 3 parts (1 on the bottom side), 16 nets.

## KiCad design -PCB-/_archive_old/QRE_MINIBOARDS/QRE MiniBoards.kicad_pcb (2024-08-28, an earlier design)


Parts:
H1, H2: M3; MountingHole_3.2mm_M3_Pad
J2: Conn_01x04_Pin; Molex_PicoBlade_53261-0471_1x04-1MP_P1.25mm_Horizontal
R1, R3: 100; R_0805_2012Metric_Pad1.20x1.40mm_HandSolder
R2, R4: 10k; R_0805_2012Metric_Pad1.20x1.40mm_HandSolder
U1, U2: QRE1113; OnSemi_CASE100AQ - QRE1113

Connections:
+3V3: J2.2, R1.2, R2.1, R3.2, R4.1
GND: H1.1, H2.1, J2.3, U1.2 (K), U1.4, U2.2 (K), U2.4
unnamed: R1.1, U1.1 (A)
unnamed: R3.1, U2.1 (A)
QRE1113 A: J2.4, R2.2, U1.3
QRE1113 B: J2.1, R4.2, U2.3

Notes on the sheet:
QRE1113 Sensors
Horizontal PicoBlade 4pin connector
MECHANICAL



Board: 2 copper layers, 90.0 x 11.0 mm, 9 parts (2 on the bottom side), 6 nets.

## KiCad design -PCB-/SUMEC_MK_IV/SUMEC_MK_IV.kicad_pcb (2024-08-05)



Board: 4 copper layers, 80.0 x 45.0 mm, 93 parts (31 on the bottom side), 68 nets.

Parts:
C1, C5, C6, C8, C10: 22uF; CP_EIA-2012-12_Kemet-R_Pad1.30x1.05mm_HandSolder
C2: 3.3nF; C_0805_2012Metric_Pad1.18x1.45mm_HandSolder
C3: 100nF.vin; C_0805_2012Metric_Pad1.18x1.45mm_HandSolder
C4: 10uF.pvin; CP_EIA-3216-18_Kemet-A_Pad1.58x1.35mm_HandSolder
C7: 100nF.avin; C_0805_2012Metric_Pad1.18x1.45mm_HandSolder
C9: 100nF.vout; C_0805_2012Metric_Pad1.18x1.45mm_HandSolder
C11, C13: 22nF; C_0805_2012Metric_Pad1.18x1.45mm_HandSolder
C12, C14, C23: 100nF; C_0805_2012Metric_Pad1.18x1.45mm_HandSolder
C15, C16: 100nF.hb; C_0805_2012Metric_Pad1.18x1.45mm_HandSolder
C17, C18: 10uF.hb; CP_EIA-3216-18_Kemet-A_Pad1.58x1.35mm_HandSolder
C19, C20: 10uF.shrp; CP_EIA-3216-18_Kemet-A_Pad1.58x1.35mm_HandSolder
C21: 10uF.mcu; CP_EIA-3216-18_Kemet-A_Pad1.58x1.35mm_HandSolder
C22: 100nF.mcu; C_0805_2012Metric_Pad1.18x1.45mm_HandSolder
C24: 100nF.en; C_0805_2012Metric_Pad1.18x1.45mm_HandSolder
C25: 100nF.boot; C_0805_2012Metric_Pad1.18x1.45mm_HandSolder
D1, D2, D7: D_Schottky; D_1206_3216Metric_Pad1.42x1.75mm_HandSolder
D3, D4, D5, D6: LED; LED_0805_2012Metric_Pad1.15x1.40mm_HandSolder
H1, H2, H3, H4: Mounting Hole M3; MountingHole_3.2mm_M3_Pad_Via
IC1: TPS565242DRLR; SOT-563
IC2, IC3: DRV8874PWPR; DRV8874
J1: XT30PW-M
J2, J5, J7, J8, J9, J11: Conn_01x03_Pin; Molex_PicoBlade_53398-0371_1x03-1MP_P1.25mm_Vertical
J3, J4, J6: Conn_01x06_Pin; Molex_PicoBlade_53398-0671_1x06-1MP_P1.25mm_Vertical
J10: Conn_01x04_Pin; Molex_PicoBlade_53398-0471_1x04-1MP_P1.25mm_Vertical
J12: Conn_01x02_Pin; TestPoint_2Pads_Pitch2.54mm_Drill0.8mm
J13: TYPE-C-31-M-12; USB_Type_C
J14, J15: Conn_01x06_Socket; JST_SH_SM06B-SRSS-TB_1x06-1MP_P1.00mm_Horizontal
L1: 1.5uH; L_Vishay_IHLP-1212
L2: 2.2uH; L_Vishay_IHLP-1616
Q1: PMOS; SOT-23-3
R1, R3, R9, R10, R11: 10k; R_0805_2012Metric_Pad1.20x1.40mm_HandSolder
R2: 45k; R_0805_2012Metric_Pad1.20x1.40mm_HandSolder
R4: 100k; R_0805_2012Metric_Pad1.20x1.40mm_HandSolder
R5, R7: 0R/R-Ipropi; R_0805_2012Metric_Pad1.20x1.40mm_HandSolder
R6, R8: 0R/R-Imode; R_0805_2012Metric_Pad1.20x1.40mm_HandSolder
R12: 100; R_0805_2012Metric_Pad1.20x1.40mm_HandSolder
R13: 560R; R_0805_2012Metric_Pad1.20x1.40mm_HandSolder
R14, R15, R16: 100R; R_0805_2012Metric_Pad1.20x1.40mm_HandSolder
R17, R18: 15R; R_0805_2012Metric_Pad1.20x1.40mm_HandSolder
R19: 10k.mcu; R_0805_2012Metric_Pad1.20x1.40mm_HandSolder
R20: R; purosidenegative
R21: R; SPS LOGO
R22: R; boi
R23: R; Logo
SW1: SW_DPDT_x2; Custom_SPDT_4.7mm_Switch
SW2, SW3, SW4, SW5: SW_Push; SW_SPST_EVQPE1
TP1, TP2, TP3, TP4: TestPoint; TestPoint_Pad_1.0x1.0mm
U1: TPS62133; VQFN-16-1EP_3x3mm_P0.5mm_EP1.68x1.68mm_ThermalVias
U2: TSOP382xx; TSOP
U3: ESP32-S3-WROOM-1
U4: USBLC6-2SC6; TSOT-23-6_HandSoldering

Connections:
+3V3: C5.1, C6.1, C8.1, C9.1, C19.1, C20.1, C21.1, C22.1, IC2.5 (VREF), IC3.5 (VREF), J2.2, J5.2, J7.2, J8.2, J9.2, J10.3, J14.4, J15.4, L1.2, R2.1, R9.1, R10.1, R11.1, R12.1, R19.2, SW4.1, SW5.1, TP1.1, U2.3 (Vs), U3.2 (3V3)
+5V: C1.1, C3.1, D1.1 (K), D2.1 (K), IC1.1 (VIN), IC1.5 (EN), J3.1, J4.1, J6.1
+12V: C4.1, C7.1, C12.2, C14.2, C15.2, C16.2, C17.1, C18.1, D3.2 (A), IC2.11 (VM), IC3.11 (VM), SW1.1 (A), U1.10 (AVIN), U1.11 (PVIN), U1.12 (PVIN), U1.13 (EN)
BOOT: C25.1, SW3.2, U3.27 (IO0)
D+: U3.14 (IO20), U4.6
D+ IN: J13.A6 (DP1), J13.B6 (DP2), R17.1
D-: U3.13 (IO19), U4.4
D- IN: J13.A7 (DN1), J13.B7 (DN2), R18.1
EN: C24.1, R19.1, SW2.2, U3.3 (EN)
FB: IC1.6 (FB), R2.2, R3.1
GND: C1.2, C2.1, C3.2, C4.2, C5.2, C6.2, C7.2, C8.2, C9.2, C10.2, C15.1, C16.1, C17.2, C18.2, C19.2, C20.2, C21.2, C22.2, C23.2, C24.2, C25.2, H1.1, H2.1, H3.1, H4.1, IC1.3 (GND), IC1.4 (AGND), IC2.9 (PGND), IC2.15 (GND), IC2.16 (PMODE), IC2.17 (EP), IC3.9 (PGND), IC3.15 (GND), IC3.16 (PMODE), IC3.17 (EP), J1.N, J2.3, J3.4, J3.5, J4.4, J4.5, J5.3, J6.4, J6.5, J7.3, J8.3, J9.3, J10.2, J11.3, J13.A1_B12 (GND), J13.B1_A12 (GND), J14.1, J15.1, R1.2, R3.2, R5.1, R6.1, R7.1, R8.1, R13.2, R14.2, R15.2, R16.2, SW2.1, SW3.1, U1.5 (FB), U1.6 (GND), U1.7 (FSW), U1.8 (DEF), U1.15 (GND), U1.16 (GND), U1.17 (GND), U2.2 (GND), U3.1 (GND), U3.40 (GND), U3.41 (GND), U4.2
IN1: IC2.2 (PH/IN2), U3.33 (IO40)
IN2: IC3.2 (PH/IN2), U3.34 (IO41)
IPROPI_ADC: IC2.6 (IPROPI), IC3.6 (IPROPI), R5.2, R7.2, U3.29 (IO36)
IR MODULE: TP4.1, U2.1 (OUT), U3.28 (IO35)
LED1: D4.2 (A), U3.23 (IO21)
LED2: D5.2 (A), U3.22 (IO14)
LED3: D6.2 (A), U3.21 (IO13)
M1A: IC2.8 (OUT1), J14.6
M1B: IC2.10 (OUT2), J14.5
M2A: IC3.8 (OUT1), J15.6
M2B: IC3.10 (OUT2), J15.5
unnamed: D1.2 (A), Q1.1 (D)
unnamed: D3.1 (K), R13.1
unnamed: D4.1 (K), R14.1
unnamed: D5.1 (K), R15.1
unnamed: D6.1 (K), R16.1
unnamed: D7.2 (A), J13.A4_B9 (VBUS), J13.B4_A9 (VBUS)
unnamed: IC1.2 (SW), L1.1
unnamed: C11.2, IC2.13 (CPH)
unnamed: C11.1, IC2.14 (CPL)
unnamed: IC2.7 (IMODE), R6.2
unnamed: C12.1, IC2.12 (VCP)
unnamed: C13.2, IC3.13 (CPH)
unnamed: C13.1, IC3.14 (CPL)
unnamed: IC3.7 (IMODE), R8.2
unnamed: C14.1, IC3.12 (VCP)
unnamed: J11.2, R12.2
unnamed: L2.1, U1.1 (SW), U1.2 (SW), U1.3 (SW)
unnamed: R17.2, U4.1
unnamed: R18.2, U4.3
unnamed: R4.2, U1.4 (PG)
unnamed: C2.2, U1.9 (SS/TR)
OUT 1A: J14.3, TP2.1, U3.18 (IO10)
OUT 1B: J14.2, TP3.1, U3.17 (IO9)
OUT 2A: J15.3, U3.19 (IO11)
OUT 2B: J15.2, U3.20 (IO12)
POL 1: J8.1, U3.5 (IO5)
POL 2: J9.1, U3.8 (IO15)
POL 3: J7.1, U3.9 (IO16)
PWM1: IC2.1 (EN/IN1), U3.35 (IO42)
PWM2: IC3.1 (EN/IN1), U3.32 (IO39)
QRE1113 A: J10.1, U3.6 (IO6)
QRE1113 B: J10.4, U3.7 (IO7)
QRE1113 C: J11.1, R11.2, U3.38 (IO2)
RX: J12.2, U3.36 (RXD0)
SCL: J3.3, J4.3, J6.3, U3.11 (IO18)
SDA: J3.2, J4.2, J6.2, U3.10 (IO17)
SHARP 1: J2.1, U3.12 (IO8)
SHARP 2: J5.1, U3.4 (IO4)
TEST PROGRAM 1: SW4.2, U3.25 (IO48)
TEST PROGRAM 2: SW5.2, U3.24 (IO47)
TX: J12.1, U3.37 (TXD0)
VBATT: J1.P, SW1.2 (B)
VBUS 5V: C23.1, D2.2 (A), D7.1 (K), Q1.2 (G), R1.1, U4.5
VOUT 5V: C10.1, L2.2, Q1.3 (S), R4.1, U1.14 (VOS)
nFAULT: IC2.4 (NFAULT), IC3.4 (NFAULT), R9.2, R10.2, U3.30 (IO37)
nSLEEP: IC2.3 (NSLEEP), IC3.3 (NSLEEP), U3.31 (IO38)

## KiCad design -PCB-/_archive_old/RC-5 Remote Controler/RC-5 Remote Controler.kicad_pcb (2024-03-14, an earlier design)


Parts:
A1: Arduino_Nano_v3.x; Arduino_Nano
D1: LED; LED_D3.0mm_Horizontal_O3.81mm_Z6.0mm
R1: 330R; R_Axial_DIN0207_L6.3mm_D2.5mm_P10.16mm_Horizontal
R2, R3, R4, R5: 10k; R_Axial_DIN0207_L6.3mm_D2.5mm_P10.16mm_Horizontal
SW1, SW2, SW3, SW4: SW_Push; SW_PUSH_6mm

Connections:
+5V: A1.27 (+5V), SW1.1, SW2.1, SW3.1, SW4.1
GND: A1.4 (GND), A1.29 (GND), D1.1 (K), R2.2, R3.2, R4.2, R5.2
unnamed: A1.5 (D2), R1.1
unnamed: A1.6 (D3), R5.1, SW1.2
unnamed: A1.7 (D4), R4.1, SW2.2
unnamed: A1.8 (D5), R3.1, SW3.2
unnamed: A1.9 (D6), R2.1, SW4.2
unnamed: D1.2 (A), R1.2


Board: 2 copper layers, 40.0 x 59.8 mm, 11 parts (0 on the bottom side), 8 nets.

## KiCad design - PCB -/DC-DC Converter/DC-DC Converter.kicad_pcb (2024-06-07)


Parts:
C1: 680uF; 12.5mm_cap
C2: 100nF; C_0805_2012Metric_Pad1.18x1.45mm_HandSolder
C3: 470uF; CP_Elec_10x12.5
D1: D_Schottky; D_1206_3216Metric_Pad1.42x1.75mm_HandSolder
L1: 46uH; L_12x12mm_H8mm
U1: TO-263-5_TabPin6

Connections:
+12V: C1.1, C2.1, U1.1 (VIN)
FB: C3.1, L1.2, U1.4 (FB)
GND: C1.2, C2.2, C3.2, D1.2 (A), U1.3 (GND), U1.5 (SD), U1.6 (TAB)
unnamed: D1.1 (K), L1.1, U1.2 (OUT)

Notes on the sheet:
DC - DC CONVERTER

Board: 2 copper layers, 6 parts (0 on the bottom side), 4 nets, no tracks yet.

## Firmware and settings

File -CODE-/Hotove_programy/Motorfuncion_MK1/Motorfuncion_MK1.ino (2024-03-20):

//important #defines
#define MOTORS_LeftSpeed 5
#define MOTORS_LeftBackward 19
#define MOTORS_LeftForward 18
#define MOTORS_RightSpeed 15
#define MOTORS_RightBackward 4
#define MOTORS_RightForward 2
#define MOTORS_STBY 23

//setup function
void MOTORS_Setup() {
  ledcSetup(0, 5000, 8);
  ledcSetup(1, 5000, 8);
  pinMode(MOTORS_LeftBackward, OUTPUT);
  pinMode(MOTORS_LeftForward, OUTPUT);
  pinMode(MOTORS_RightBackward, OUTPUT);
  pinMode(MOTORS_RightForward, OUTPUT);
  pinMode(MOTORS_STBY, OUTPUT);
  ledcAttachPin(MOTORS_LeftSpeed, 0);
  ledcAttachPin(MOTORS_RightSpeed, 1);
}

//brake function
void MOTORS_Brake() {
  digitalWrite(MOTORS_LeftForward, LOW);
  digitalWrite(MOTORS_RightForward, LOW);
  digitalWrite(MOTORS_LeftBackward, LOW);
  digitalWrite(MOTORS_RightBackward, LOW);
  ledcWrite(0, 255);
  ledcWrite(1, 255);
  digitalWrite(MOTORS_STBY, HIGH);
}



//universal motors function
//ex.: MOTORS_Go([SpeedLeft], [SpeedRight]);
//speed can be from -255 to 255

void MOTORS_Go(int MOTORS_SpeedLeft, int MOTORS_SpeedRight) {

  if (MOTORS_SpeedLeft < -255) {  //left motor speed cap -
    MOTORS_SpeedLeft = -255;
  } else if (MOTORS_SpeedLeft > 255) {  //left motor speed cap +
    MOTORS_SpeedLeft = 255;
  }

  if (MOTORS_SpeedLeft < 0) { //if left motor set to go backward
    digitalWrite(MOTORS_LeftForward, LOW);
    digitalWrite(MOTORS_LeftBackward, HIGH);
  } else  if (MOTORS_SpeedLeft > 0) { //if left motor set to go forward
    digitalWrite(MOTORS_LeftForward, HIGH);
    digitalWrite(MOTORS_LeftBackward, LOW);
  } else {  //else left motor will stop
    digitalWrite(MOTORS_LeftForward, LOW);
    digitalWrite(MOTORS_LeftBackward, LOW);
    MOTORS_SpeedLeft = 255;
  }
  

  if (MOTORS_SpeedRight < -255) { //right motor speed cap -
    MOTORS_SpeedRight = -255;
  } else if (MOTORS_SpeedRight > 255) { //right motor speed cap +
    MOTORS_SpeedRight = 255;
  }

  if (MOTORS_SpeedRight < 0) {  //if right motor set to go backward
    digitalWrite(MOTORS_RightForward, LOW);
    digitalWrite(MOTORS_RightBackward, HIGH);
  } else  if (MOTORS_SpeedRight > 0) {  //if right motor set to go forward
    digitalWrite(MOTORS_RightForward, HIGH);
    digitalWrite(MOTORS_RightBackward, LOW);
  } else {  //else right motor will stop
    digitalWrite(MOTORS_RightForward, LOW);
    digitalWrite(MOTORS_RightBackward, LOW);
    MOTORS_SpeedRight = 255;
  }

  if (MOTORS_SpeedLeft < 0) { //if left motor backward
    MOTORS_SpeedLeft = MOTORS_SpeedLeft * -1; //speed *-1 because negative numbers can't be used
  }

  if (MOTORS_SpeedRight < 0) {  //if right motor backward
    MOTORS_SpeedRight = MOTORS_SpeedRight * -1; //speed *-1 because negative numbers can't be used
  }

  ledcWrite(0, MOTORS_SpeedLeft); //set speed for left motor
  ledcWrite(1, MOTORS_SpeedRight);  //set speed for right motor
  digitalWrite(MOTORS_STBY, HIGH);  //set standby to high
}


void setup() {
  MOTORS_Setup();

}

void loop() {
  MOTORS_Go(255, 255);
}

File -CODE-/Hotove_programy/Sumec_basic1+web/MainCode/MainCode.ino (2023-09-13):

/*|Start of imports||Start of imports||Start of imports||Start of imports||Start of imports||Start of imports|*/
#include <WiFi.h>
#include <WebServer.h>
#include <WebSocketsServer.h>
#include <ArduinoJson.h>
#include "laser.h"
#include "line.h"

/*|End of imports||End of imports||End of imports||End of imports||End of imports||End of imports||End of imports|*/
/*|Webserver and AP stuff||Webserver and AP stuff||Webserver and AP stuff||Webserver and AP stuff||Webserver and AP stuff||Webserver and AP stuff||Webserver and AP stuff||Webserver and AP stuff||Webserver and AP stuff|*/
TaskHandle_t Task1;

int Global_RunButtonPressed = 0;
int Global_ModeSelectVar = 0;

const char* ssid = "Sumec_#01";			/*sumec's ap ssid*/
const char* password = "SumecPass1";	/*sumec's ap pass*/
IPAddress local_IP(182,168,1,22);		/*sumec's local ip*/

IPAddress gateway(182,168,1,5);
IPAddress subnet(255,255,255,0);

WebServer server(80);
WebSocketsServer webSocket = WebSocketsServer(81);

String webpage = "<!DOCTYPE html><html style = 'font-family:consolas; line-height:0.7;'><head><title>Sumec's main control</title></head><body><h1>Sumec_In</h1><h2>Mode: <select name='Mode_Select' id='ModeSelect'><option value='0'>Stop</option><option value='1'>Normal</option><option value='2'>Debug</option></select><button type='button' id='RunButton'>Run</button></h2><h3>Curent: <span id='CurrentMode'>-</span></h3><br><h1>Sumec_Out</h1><h2>VL53L0X sensors (distance)</h2><h3>Range: <span id='Dist_Range'>-</span></h3><table style='width:100%' border= 1px;><tr><th><h3>Left:</h3></th><th><h3>Front:</h3></th><th><h3>Right:</h3></th></tr><tr><th><span id='Dist_Left'>-</span></th><th><span id='Dist_Front'>-</span></th><th><span id='Dist_Right'>-</span></th></tr></table><h2>QRE1113 sensors (line)</h2><h3>Threshold: <span id='Line_Thre'>-</span></h3><table style='width:100%' border= 1px;><tr><th><h3>Front left:</h3></th><th><h3>Front right:</h3></th></tr><tr><th><span id='Line_FL'>-</span></th><th><span id='Line_FR'>-</span></th></tr><tr><th><h3>Back left:</h3></th><th><h3>Back right:</h3></th></tr><tr><th><span id='Line_BL'>-</span></th><th><span id='Line_BR'>-</span></th></tr></table><h2>Code pos.</h2><h3><span id='Code_Pos'>-</span></h3></body><script>var Socket;document.getElementById('RunButton').addEventListener('click', button_send_back);function init() {Socket = new WebSocket('ws://' + window.location.hostname + ':81/');Socket.onmessage = function(event) {processCommand(event);};}function button_send_back() {var SendObj = {RunButton: '1',ModeSelectVar: document.getElementById('ModeSelect').value};Socket.send(JSON.stringify(SendObj));}function processCommand(event) {var obj = JSON.parse(event.data);document.getElementById('CurrentMode').innerHTML = obj.CurrentMode;document.getElementById('Dist_Range').innerHTML = obj.Dist_Range;document.getElementById('Dist_Left').innerHTML = obj.Dist_Left;document.getElementById('Dist_Front').innerHTML = obj.Dist_Front;document.getElementById('Dist_Right').innerHTML = obj.Dist_Right;document.getElementById('Line_Thre').innerHTML = obj.Line_Thre;document.getElementById('Line_FL').innerHTML = obj.Line_FL;document.getElementById('Line_FR').innerHTML = obj.Line_FR;document.getElementById('Line_BL').innerHTML = obj.Line_BL;document.getElementById('Line_BR').innerHTML = obj.Line_BR;document.getElementById('Code_Pos').innerHTML = obj.Code_Pos;console.log(obj.CurrentMode);console.log(obj.Dist_Range);console.log(obj.Dist_Left);console.log(obj.Dist_Front);console.log(obj.Dist_Right);console.log(obj.Line_Thre);console.log(obj.Line_FL);console.log(obj.Line_FR);console.log(obj.Line_BL);console.log(obj.Line_BR);console.log(obj.Code_Pos);}window.onload = function(event) {init();}</script></html>";

int interval = 500;
unsigned long prevoiusMillis = 0;

StaticJsonDocument<400> JsonDoc_tx;
StaticJsonDocument<400> JsonDoc_rx;

void webSocketEvent (byte num, WStype_t type, uint8_t * payload, size_t length) {
	switch (type) {
		case WStype_DISCONNECTED:
			Serial.print("Core ["); Serial.print(xPortGetCoreID()); Serial.print("]: ");
			Serial.print("Client #");
			Serial.print(num);
			Serial.println(" Disconnected");
			break;
		
		case WStype_CONNECTED:
			Serial.print("Core ["); Serial.print(xPortGetCoreID()); Serial.print("]: ");
			Serial.print("Client #");
			Serial.print(num);
			Serial.println(" Connected");
			break;
		
		case WStype_TEXT:
			DeserializationError error = deserializeJson(JsonDoc_rx, payload);
			if(error) {
				Serial.print("Core ["); Serial.print(xPortGetCoreID()); Serial.print("]: ");
				Serial.println("deserializeJson() failed");
				return;
			}
			else {	/*recieve*/
				const char* RunButton = JsonDoc_rx["RunButton"];
				const int ModeSelectVar = JsonDoc_rx["ModeSelectVar"];
				
				Global_RunButtonPressed = String(RunButton).toInt();
				Global_ModeSelectVar = String(ModeSelectVar).toInt();
				Serial.print("Core ["); Serial.print(xPortGetCoreID()); Serial.print("]: ");
				Serial.println(RunButton);
				Serial.print("Core ["); Serial.print(xPortGetCoreID()); Serial.print("]: ");
				Serial.println(ModeSelectVar);
			}
			break;
	}
}
/*|Webserver and AP stuff||Webserver and AP stuff||Webserver and AP stuff||Webserver and AP stuff||Webserver and AP stuff||Webserver and AP stuff||Webserver and AP stuff||Webserver and AP stuff||Webserver and AP stuff|*/

String Global_CurrentMode = "[starting]";			/*mode*/
String Global_Dist_Range = "Empty";			/*distance sensors*/
String Global_Dist_Left = "Empty";			/*distance sensors*/
String Global_Dist_Front = "Empty";			/*distance sensors*/
String Global_Dist_Right = "Empty";			/*distance sensors*/
String Global_Line_Thre = "Empty";				/*line sensors*/
String Global_Line_FL = "Empty";				/*line sensors*/
String Global_Line_FR = "Empty";				/*line sensors*/
String Global_Line_BL = "Empty";				/*line sensors*/
String Global_Line_BR = "Empty";				/*line sensors*/
String Global_Code_Pos = "Nothing yet";			/*code pos*/
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

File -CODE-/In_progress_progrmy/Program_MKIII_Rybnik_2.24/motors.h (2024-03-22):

//important #defines
#define MOTORS_LeftSpeed 14
#define MOTORS_Left 12
#define MOTORS_RightSpeed 21
#define MOTORS_Right 13
#define nSLEEP 11

//setup function
void MOTORS_Setup() {
  pinMode(MOTORS_Left, OUTPUT);
  pinMode(MOTORS_Right, OUTPUT);
  ledcAttachPin(MOTORS_LeftSpeed, 0);
  ledcAttachPin(MOTORS_RightSpeed, 1);
  pinMode(nSLEEP, OUTPUT);
}



void MOTORS_Go(int MOTORS_SpeedLeft, int MOTORS_SpeedRight) 
{

  if(MOTORS_SpeedLeft > 0)
  {
    analogWrite(MOTORS_LeftSpeed, MOTORS_SpeedLeft);
    digitalWrite(MOTORS_Left, LOW);
  }
  if(MOTORS_SpeedLeft == 0)
  {
    analogWrite(MOTORS_LeftSpeed, 0);
    digitalWrite(MOTORS_Left, LOW);
  }
  if(MOTORS_SpeedLeft < 0)
  {
    analogWrite(MOTORS_LeftSpeed, (MOTORS_SpeedLeft*-1));
    digitalWrite(MOTORS_Left, HIGH);
  }


  if(MOTORS_SpeedRight > 0)
  {
    analogWrite(MOTORS_RightSpeed, MOTORS_SpeedRight);
    digitalWrite(MOTORS_Right, HIGH);
  }
  if(MOTORS_SpeedRight == 0)
  {
    analogWrite(MOTORS_RightSpeed, 0);
    digitalWrite(MOTORS_Right, LOW);
  }
  if(MOTORS_SpeedRight < 0)
  {
    analogWrite(MOTORS_RightSpeed, (MOTORS_SpeedRight*-1));
    digitalWrite(MOTORS_Right, LOW);
  }

  digitalWrite(nSLEEP, HIGH);
  
}

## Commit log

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2023-05-23 PCB and DOCS update: Page structure (WIP) and BOM
    [aktuální seznam.xlsx, sumec.kicad_sch, unsensors.kicad_sch]
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2023-05-23 PCB - SCH UPDATE (fully labelled and described)
    [MCU.kicad_sch, MECHANICS.kicad_sch, POWER SUPPLY.kicad_sch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]
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2023-05-25 Revert "Update SENSORS.kicad_sch"
    This reverts commit 14cb2c9d299c5770f96d1d2006461c26369d9e88.
    [SENSORS.kicad_sch]
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2023-05-25 PCB - sch and footprint update, QRE1113 3D model.
    [MECHANICS.kicad_sch, POWER SUPPLY.kicad_sch, SENSORS.kicad_sch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]
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2023-05-25 PCB - board update + footprint/3d models export
    [MCU.kicad_sch, MECHANICS.kicad_sch, POWER SUPPLY.kicad_sch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]
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2023-06-08 PCB - Wiring control and fix
    [sumec.kicad_pcb]
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2023-06-16 Github bug
    [SUMEC FULL BOM.xlsx]
2023-06-16 Github bug fix (BOM)
    [Full BOM.xlsx]
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2023-06-19 PCB - Pad size fix (riveting)
    [sumec.kicad_pcb]
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2023-08-20 LOGO LETSS GGOOO WOOAH YEAAAAH
    holy moly logo darg wizzarddry shit, its so fire LETSS GOOO
    [MCU.kicad_sch, sumec.kicad_pcb, sumec.kicad_sch]
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2023-09-11 Custom Wheels update and PCB comp. naming update
    [JS2622 - Wheels (no silicon).ipt, MCU.kicad_sch, POWER SUPPLY.kicad_sch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]
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2023-09-19 PCB SMD - WIP ESP32 S3 WROOM 2
    [MCU.kicad_sch, MECHANICS.kicad_sch, POWER SUPPLY.kicad_sch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]
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2023-10-20 3D model jst - 1 mm 6 pin female
    [TF-LC02 (Laser senzor) s konektorem.0002.iam, TF-LC02 (Laser senzor) s konektorem.iam, jst - 1 mm 6 pin female (NEPOUŽITELNÝ).ipt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]
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2023-10-20 PCB cooler schematic and start of board making
    bettr cal sol
    [MCU.kicad_sch, MECHANICS.kicad_sch, POWER SUPPLY.kicad_sch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]
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2023-10-25 Fixed mission critical errror with smd pcb that savva couldn't fix
    [sumec.kicad_pcb]
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2023-10-29 Minor redesign
    Distance sensor connector pin order chenged, LDO regulator heat pads added, mounting holes layout changed
    [MCU.kicad_sch, MECHANICS.kicad_sch, POWER SUPPLY.kicad_sch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]
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2023-11-13 Revert "cg dcg cgcvcgncgjcgcgjfuckthisshit hnmmhnvvm bvm"
    This reverts commit fd7afdc58fbd80746bbebdeea76158c0cdb7aa1a.
    [SetAddress.ino]
2023-11-13 Revert "Revert "cg dcg cgcvcgncgjcgcgjfuckthisshit hnmmhnvvm bvm""
    This reverts commit daf0b0849d3f191dacdd118931538dce37c0c081.
    [SetAddress.ino]
2023-11-13 Revert "M HKGH"
    This reverts commit d9fa6ff84e2bc00fc898a878a55807f7b7556152, reversing
    changes made to 8cebf9d8a72c06353403efe62b93bffaf47f05be.
    [C_1206_3216Metric.0001.iam, C_1206_3216Metric.iam, D_1206_3216Metric.0001.iam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]
2023-11-13 Revert "Revert "M HKGH""
    This reverts commit 82dfd9ffbfe74170be4ed8f6845d988fec4efd35.
    [C_1206_3216Metric.0001.iam, C_1206_3216Metric.iam, D_1206_3216Metric.0001.iam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]
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2023-11-24 Revert "Merge branch 'sumec-main' of https://github.com/menmenson/RoboCop into sumec-main"
    This reverts commit c12e1b1a68497c267c3f967de85c9fbdb80dadfd, reversing
    changes made to c4b67ce6a8d4b2794d885fa28f21522aaf6bc740.
    [Program_sumec2HW-tlac.ino, Program_sumec2hardware.ino, main.cpp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]
2023-11-24 Revert "bom"
    This reverts commit c4b67ce6a8d4b2794d885fa28f21522aaf6bc740.
    [Full BOM.xlsx, bom.xlsx]
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2023-12-01 Revert "Merge branch 'sumec-main' of https://github.com/menmenson/RoboCop into sumec-main"
    This reverts commit dbf205ac3b02d72b1b38e86a27b286e1b118f9d4, reversing
    changes made to f2387d167bca73d6a0741a06b82f65a42dfb555a.
    [POWER SUPPLY.kicad_sch, QRE MiniBoards.kicad_pcb, QRE MiniBoards.kicad_sch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]
2023-12-06 Sensors replace
    [Sensor LUNA.STEP, Sensor LUNA.STL, Sensor LUNA.ipt]
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2023-12-11 motor fixes
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2024-01-26 minor fixes; removed the address setting func from lunas auto
    [FunkceTfLEsp32S3Automatic.ino, SetAddressesNew.ino]
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2024-01-31 Updates:
    GyroScope project file, QRE1113 Board update and BOM, SMDv2 iBOM and schematic update.
    [Gyros-Scope.kicad_pcb, Gyros-Scope.kicad_sch, MCU.kicad_sch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]
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2024-02-10 NotMuch
    fixed my name in SENSORS
    work on the WSRCP
    [MCU.kicad_sch, MECHANICS.kicad_sch, POWER SUPPLY.kicad_sch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]
2024-02-11 mateji co jsi kurva delal v slozce PCB??
    [MCU.kicad_sch, MECHANICS.kicad_sch, POWER SUPPLY.kicad_sch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]
2024-02-11 Revert "mateji co jsi kurva delal v slozce PCB??"
    This reverts commit db6b80f6998ca08dcf5bbaff0895d0cea7c46a95.
    [MCU.kicad_sch, MECHANICS.kicad_sch, POWER SUPPLY.kicad_sch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]
2024-02-11 Revert "NotMuch"
    This reverts commit 5cbd2642644b9284d81b9cce7fefcd6497c1fb2a.
    [MCU.kicad_sch, MECHANICS.kicad_sch, POWER SUPPLY.kicad_sch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]
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2024-02-11 Revert "please at to funguje"
    This reverts commit e21140d7c75849dc3e7005e9cafbacb66198ee39.
    [MCU.kicad_sch, MECHANICS.kicad_sch, POWER SUPPLY.kicad_sch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]
2024-02-11 fuckup reverted???
    [EXTERNAL.kicad_sch, MCU.kicad_sch, MECHANICS.kicad_sch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]
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2024-02-18 added print for deserialization error
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2024-02-23 PCB Update, Buzzer, DRC.
    [MCU.kicad_sch, MECHANICS.kicad_sch, POWER SUPPLY.kicad_sch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]
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2024-02-24 step update delete of buzzer
    [MCU.kicad_sch]
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2024-02-28 BOM LED replacement
    [Complete BOM.xlsx, SUMEC-V2 mouser BOM.xls]
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2024-03-01 Added WebServer; check for bugs and errors
    [FunkcniFunkceCaryEsp32S3.ino, Program_sumec2hardware-webserver.ino, rogram_sumec2HW_promene.h]
2024-03-01 last push had a mistake; now fixed
    [Program_sumec2hardware-webserver.ino, rogram_sumec2HW_promene.h]
2024-03-01 Discovery of KiCAD 8 (the UI is broken?)
    [MCU.kicad_sch, MECHANICS.kicad_sch, POWER SUPPLY.kicad_sch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]
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2024-03-06 PCB - NO CHANGES, Additional BOM added
    Cleanup of obsolete BOMs
    [Additonal BOM mouser.xls, Additonal BOM.xlsx, Complete BOM mouser.xls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]
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2024-03-06 bacjk qre flex mount
    [Sestava.0025.iam, Sestava.0026.iam, Sestava.iam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]
2024-03-07 qre flex mount update
    [Sestava.0026.iam, Sestava.0027.iam, Sestava.iam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]
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2024-03-12 flex parts
    [Sestava.0030.iam, Sestava.0031.iam, Sestava.iam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]
2024-03-12 motor clamp fix
    [motor_C_clamp_nutt_motor_otoceny.0005.ipt, motor_C_clamp_nutt_motor_otoceny.0006.ipt, motor_C_clamp_nutt_motor_otoceny.ipt]
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2024-03-18 back qre mount fix
    [back qre flex holder.0003.ipt, back qre flex holder.0005.ipt, back qre flex holder.ipt]
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2024-03-20 fix for mk3
    will change the whole sorting from by processor to by pcb ver. :3
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2024-03-21 base_plate_isolation fix
    [base_plate_isolation.0001.ipt, base_plate_isolation.0002.ipt, base_plate_isolation.ipt]
2024-03-23 Fixed wrong pin for FRONT LEFT sensor with DIGITAL out
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2024-03-23 added i2c scanner and tfl lib tfl lib has only set addr and factory reset
    [I2CScanner.ino, TF-Luna.ino]
2024-03-26 added small ReadMe(s) to new function test directories, added more comments to new functions, fixed code formatting notes: TF-L function needs more comments; there weren't many code formatting issues
    [DRV8874PWPR.h, Sharp_GP2Y0D810Z0F.ino]
2024-03-27 fix for legacy tf-l code
    [SetAddressesNew.ino]
2024-03-27 fixed left motor being reversed
    [DRV8874PWPR.h, DRV8874PWPR.ino]
2024-03-27 fixed wrong threshold data-type; added .getRaw()
    [QRE1113.ino]
2024-03-27 Driver test fix; Qre and Sharp libs pinMode fix
    [DRV8874PWPR.ino]
2024-03-27 tf-l set address and factory reset work, read and read distance do not
    [TF-Luna.ino]
2024-03-28 Driver lib wrong ledc channel fix both of the ledc channels could not be changed and both were set to 0 by default
    [DRV8874PWPR.h, DRV8874PWPR.ino]
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2024-05-22 box flex parts STLs
    [botom_insert.stl, sumec_box-seal.0001.ipt, sumec_box-seal.ipt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]
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2024-07-01 Start of DRV Breakout board
    should be an easy one
    [DRV_BREAKOUT_BOARD.kicad_pcb, DRV_BREAKOUT_BOARD.kicad_sch]
2024-07-01 Change of folder path. breakout board for DRV driver
    [Additonal BOM mouser.xls, Additonal BOM.xlsx, COMPOUND.ipt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]
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2024-07-01 github cleanup. folder renaming. pcb folder cleanup.
    Pics do not belong in github, dont worry, still have them on my machine.
    [2s lipo.ipt, 3s lipo.0001.ipt, 3s lipo.ipt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]
2024-07-04 i did, something (archive return but now its better)
    [ABM8G-16.000MHZ-18-D2Y-T.stp, Additonal BOM mouser.xls, Additonal BOM.xlsx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]
2024-07-05 heyyo not much done, just me, goofing arounf
    hwy i wish i wasnt thee only oen taking this project seriosly, its quite a shame that a lot of mechanics guysss almost gave up on it, like, im drunk adn im working on it, thats probably very sad actu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
    [MCU.kicad_sch]
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2024-07-05 at the crib, straight up "working it" and by "it" hehe, lets just say, my KiCADIS
    [MCU.kicad_sch]
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2024-07-11 MK_IV update
    Power supp sheet done, mechanical sheet almost done, some changes, updates etc.
    [CONNECTIVITY.kicad_sch, GRAPHICS.kicad_sch, MCU.kicad_sch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]
2024-07-11 Schematic update
    Motor driver rework, more functions and options added.
    [MOTOR_CONTROL.kicad_sch]
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2024-07-13 MK4 schematic update
    Almost done. Did some work on motor drivers, should be final now. Sensors sheet is almost done - object detecting missing. MCU sheet - missing. but yeah. almost done.
    [MCU.kicad_sch, MECHANICS.kicad_sch, MOTOR_CONTROL.kicad_sch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]
2024-07-14 MKIV update
    Updated sensors sheet, did some research, updated mcu. Almoooost done. Gotta take a walk with da dog.
    [MCU.kicad_sch, SENSORS.kicad_sch]
2024-07-15 MKIV major update
    Updated everything, custom symbol for ESP32, MCU sheet done, new test points added, motor control revision.
    all left is to clean it up a bit
    [CONNECTIVITY.kicad_sch, GRAPHICS.kicad_sch, MCU.kicad_sch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]
2024-07-16 3v3 buck redesign
    [MCU.kicad_sch, MECHANICS.kicad_sch, MOTOR_CONTROL.kicad_sch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]
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2024-08-02 PCB update
    (should I start over? Can I make it better)
    [MCU.kicad_sch, SUMEC_MK_IV.kicad_pcb]
2024-08-05 v3.0.9 SUMEC PCB
    Ufff, so, basically a full rewrite of the PCB, check it our its pretty sick, I think
    [CONNECTIVITY.kicad_sch, GRAPHICS.kicad_sch, MCU.kicad_sch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]
2024-08-06 DRC Hell fix
    [GRAPHICS.kicad_sch]
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2024-08-24 New models, TSOP positioning
    new 3d models thx jonas
    [SPDT_Switch_piano_noHoles.stp, TSOP382.stp, TSOP382_1.stp]
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2024-08-28 Moved REMOTE pcb from sumec repo to the remote
    [Remote-B_Cu.gbl, Remote-B_Mask.gbs, Remote-B_Paste.gbp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]
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2024-08-30 Dimensions back and front, 3d models for footprints.
    [CONNECTIVITY.kicad_sch, MCU.kicad_sch, MOTOR_CONTROL.kicad_sch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]
2024-09-03 PCB and BOM updates
    Added links to MK_IV bom
    Fixed PMOS position and same length USB traces
    [After_Rybnik_BOM.xlsx, CONNECTIVITY.kicad_sch, MCU.kicad_sch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]
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2024-09-06 Calendar creation
    Added a word doc for Robotic tournaments for SUMEC and [line follower] to compete in.
    [MK_IV bom.xlsx, old_After_Rybnik_BOM.xlsx, old_Reserve BOM.xlsx]
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2024-09-15 Schematic and PCB update
    Schematic update:
    - Font adjustment
    - Block rearrangement
    PCB update
    - Silkscreen
    - Minor layout update
    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
    [CONNECTIVITY.kicad_sch, GRAPHICS.kicad_sch, MCU.kicad_sch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]
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2024-09-16 minor text update in schematic
    Updated wrong branch but its fixed now
    [CONNECTIVITY.kicad_sch, POWER_SUPPLY.kicad_sch, SUMEC_MK_IV.kicad_sch]
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2024-09-20 3d filepath fix, long filepath fix
    [CONNECTIVITY.kicad_sch, GRAPHICS.kicad_sch, MCU.kicad_sch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]
2024-09-20 fixing Savva's filepath mistakes
    he's a little dumb so it's fixed now. replaced his local path to some(usb-c, xt30, esp, tosp, drv874, pwr switch) 3d models with the relative project path
    UwU
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2024-09-22 3D-temporary testing body
    version of the body 3d model dedicated for testing new motors with old PCB
    [body - kopie.0047.ipt, body-motor_test_prototipe.ipt, main_sumec_assembly.0010.iam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]
2024-09-22 Some minor changes
    BOM update, checked for some pinouts, still some work to do
    [CONNECTIVITY.kicad_sch, GRAPHICS.kicad_sch, MCU.kicad_sch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]
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2024-09-25 BOM Update
    PMOS link fix
    [MK_IV bom.xlsx]
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2024-09-27 test body PCB mount fix
    [body-motor_test_prototipe.0048.ipt, body-motor_test_prototipe.0049.ipt, body-motor_test_prototipe.ipt]
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2024-09-29 PCB Update
    DRC fix with 3v3 stepdown
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2024-09-30 new fixed gerber
    [SUMEC_MK_IV-B_Cu.gbl, SUMEC_MK_IV-B_Mask.gbs, SUMEC_MK_IV-B_Paste.gbp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]
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2024-10-27 USB footprint fix
2024-11-02 Main MOSFET switch fix
    [POWER_SUPPLY.kicad_sch]
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2024-11-15 USB C - fix
    [CONNECTIVITY.kicad_sch, GRAPHICS.kicad_sch, MCU.kicad_sch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]
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2024-11-17 PCB USB C fix + silkscreen fix
    [MCU.kicad_sch, POWER_SUPPLY.kicad_sch]
2024-11-17 PCB Mosfet trace fix, test points
    [CONNECTIVITY.kicad_sch, GRAPHICS.kicad_sch, MCU.kicad_sch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]
2024-11-20 all fixed ready to export
    [GRAPHICS.kicad_sch]
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2024-12-13 Schematic PDFs - Nats issue fixed
    [Additonal BOM mouser.xls, Additonal BOM.xlsx, COMPOUND.ipt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]
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2025-02-16 new PCB start
    Yeah yeah I know, pushing into main, it'll be dealt with once I create PCB repo
    [CONNECTIVITY.kicad_sch, GRAPHICS.kicad_sch, MCU.kicad_sch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]
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
